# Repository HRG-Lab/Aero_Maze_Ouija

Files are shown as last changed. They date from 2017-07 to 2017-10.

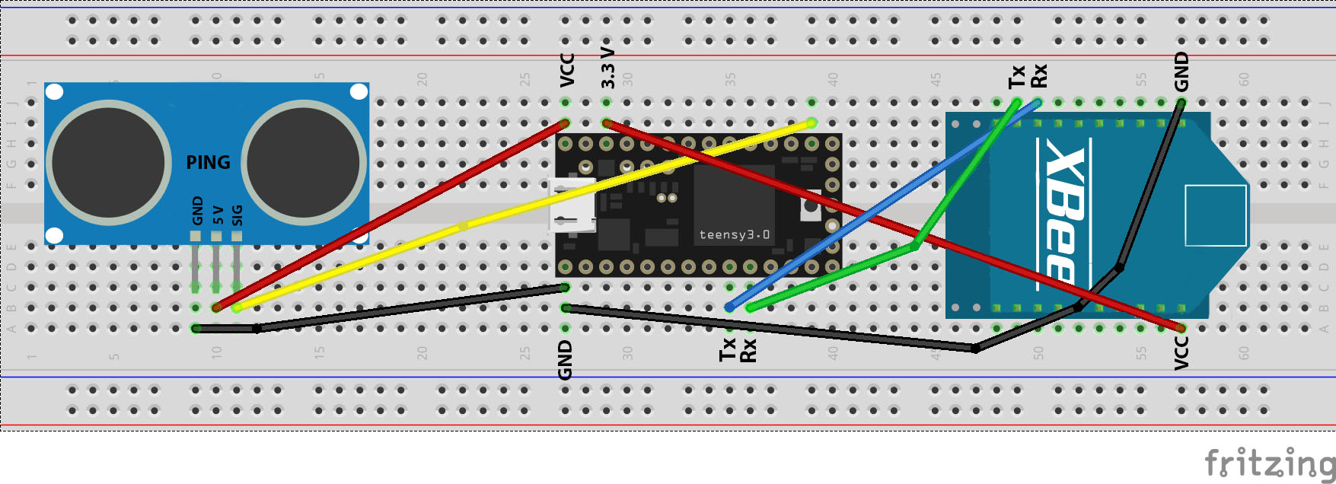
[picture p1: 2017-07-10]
Documentation/Ping_Sensor_Transmitter.jpg

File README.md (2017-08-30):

# Aero_Maze_Ouija #

### Description ###
The Aero Maze Ouija is an apparatus consisting of a group of sensors coordinating a hexacopter whose main body is a marble maze.
The project is intended to be used as a teambuilding exercise. The game, as designed, is meant for six players.
Each player will be assigned a distance sensor which will be used to measure the length between the sensor and each player's hand.
This data is then sent to the drone and mapped to a PWM value to control the speed of each motor.
Each of the six motors is linked to one specific sensor, so each player will be in control of one propeller.
There will be a maze etched into the drone where there will be a marble or bb.
The goal of the game is to work as a team and navigate the marble through the maze by controlling the orientation of the drone.

drone-overview

- - - -

## Required Software and Libraries ##
* Arduino v1.8.1
* XCTU to setup Xbee's
* Autodesk Fusion 360 (Optional, but you can size the maze we designed)
* Arduino Libraries:
  * Teesnyduino
  * EasyTransfer Library
  
- - - -

## Required Hardware ##
* A body for your drone, preferably made out of fiberglass
* 6 Turnigy Aerodrive D3536/9 910 KV Motors
* 6 Mounts designed for the Turnigy motors
* 6 Propellers, we used 3 1045's and 3 1045R's
* 6 Metal U channels
* An assortment of screws
* 7 xBees
* 6 ESC's, we used 6 Hobby King 30A UBEC's
* 3 Leg stands to attach to the U channels
* Xbee explorer board to
* Breadboard to mount electronics
* At least 8 pairs of XT60 connectors and the corresponding wires

- - - -

## Tools Needed for Assembly ##

* CNC Router to sketch the maze
* Power tools needed to drill holes etc.

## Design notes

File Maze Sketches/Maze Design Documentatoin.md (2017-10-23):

## Designing The Maze ##

* Using the software Autodesk Fusion 360 we have designed a marble maze that is based upon a Smith chart. Using the parameters menu one can easily reconfigure the size and dimensions of the maze to fit the almost any size board. One can easily find the software underneath Autodesk’s official website and receive a one month free trial to quickly generate an STL underneath any size they wish. The STL we have included in our files is a maze designed for a 14 inch diameter round piece of wood.

## Modifying the Maze ##

* In Autodesk Fusion 360, open the parameters menu and the main parameters the user will want to modify will be:
	* body_diameter - Set the diameter of your wood
	* trough_width - Set the width of the guiding structures of the maze
	* trough_depth - Set the depth of the guiding structures
	* end_hole_depth - Set the depth of the center hole in the maze
	* distance_guide - Is approximately the distance between the center of the neighboring guiding structure and the guiding structure that the former cuts off. One should tinker with this parameter to get the correct dimensions for their maze.

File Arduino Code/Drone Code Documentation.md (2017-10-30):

### Required Software ###
 
* Arduino 1.8.3 (https://www.arduino.cc/en/main/software)
* Teensyduino (https://www.pjrc.com/teensy/teensyduino.html)
* EasyTransfer Library (https://github.com/madsci1016/Arduino-EasyTransfer)
* XCTU (Source 8)
* AutoCAD Fusion 360 (https://www.autodesk.com/products/fusion-360/overview)
* Anaconda
* Pycharm
* PySerial

- - - -
 
## Setting up Software ##
 
* You will need to download and install Arduino 1.8.3 onto your computer if you do not already have Arduino installed. Leave all settings as default. Open up Arduino and try uploading a blank code to your device, or maybe a simple blink program. Make sure the right board is selected by going to Tools->Board:-> and select the device you are trying to upload the code to, such as Arduino Genuino/Uno, Teensy LC, or Teensy 3.0. 
* For Teensy 3.0 and Teensy LC it is necessary to have the Teensyduino downloaded. Do not change any of the settings or file locations when downloading Teensyduino, everything will be automatically setup for you.  When using Teensy 3.0 it will be necessary to change the frequency of the device by going to `Tools->CPU Speed:->` and changing it from 96 MHz (overclocked) to 48 MHz to avoid damaging the device. 
* The library EasyTransfer will need to be downloaded for this project and installed in the correct file. To do this find your Arduino folder stored in your hard drive at a location such as `c/Program Files (x86)/Arduino/library` and copy the unzipped EasyTransfer library into the library folder. 
* To configure the XBee’s you will need to have XCTU downloaded and installed on your computer. Download the latest version of XCTU and install it on your computer without changing any of the default settings. 

- - - -

### Motor Testing ###
* To test motors, wire pin 9 of the Arduino to the signal wire of the ESC and the ground wire of the Arduino to the ground wire of the ESC. Also, attach the servomotor and the power supply to the ESC. 

    
    
    *Pictured Above: Wiring of Servo Motor for testing*

* Upload the code to the Arduino and open the serial monitor. Type in a value and your motor’s speed will gradually rise or fall to match your entered value.

- - - -

## Programmming the ESC’s ##

* The arduino file underneath the filepath: `Arduino Code/Program ESC/ESCProgrammer/ESCProgrammer.ino` is designed to program the electronic speed controllers so that when the ESC’s are controlling the speed of the motors, the motors will turn on at roughly the same value and spin at similar rates.

1. Plug in an arduino to your computer and attach the ground port on the arduino to the ground pin (black wire) on the ESC PWM wires and port 9 on the arduino to the signal pin (white wire) on the ESC PWM wires. Also, attach power wires to the ESC.

    
    
    *Pictured Above: how to configure wires to ESC to program*

2. Before uploading the code, disconnect and reconnect the power supply to the ESC, this will allow the ESC to be programmed. Upload the code located in the aforementioned file path and upload this onto the board. Open the serial monitor and wait for the text “Done” to appear.

3. Repeat these steps on all the ESC’s until all are programmed.

- - - -

## Configure XBee setup ##

* Once XCTU installed connect the XBee using the XBee Explorer Dongle and open XCTU. Click on “Discover Radio Modules connected to your machine” and select the USB serial ports that show up. Click Next and then Click finish. If the device does not show up the first time you may need to select more Baud rates before clicking finish. Click “Add selected devices”, and then click on the selected device to configure it and access the console. The configuration settings used are pictured below. 

    
    
    *Pictured Above: The Settings window for XBee module displaying the settings we used*

* The only thing that was changed from the default was changing the Network ID from 7FFF to 8FFF. To communicate between two XBees select the console tab which is located right next to the settings tab and click the “Open/Close” button. This allows for you to see the messages sent by other networks on you console screen and send messages from the console screen to other XBees in the same network.

    
    
    *Pictured Above: Console window showing two XBees communicating with each other. The red text is from the other XBee, while the blue text is from the XBee that is connected to your device*

- - - -

## Configure Distance Transmission Setup ##

### Distance Sensor Setup ###

* Using a Teensy 3.0 or Teensy LC connect the distance sensor that is being used according to the following setup: Connect the GND pins to each other, the 5V pin to Vin on Teensy 3.0 or 5V on Teensy LC or Arduino Uno. Connect the signal pin (for the parallax 28015 ping ultrasonic range finder it is labeled SIG and for the XL-MaxSonar –EZ/AE Ultrasonic range finder it is pin 3) to an analog pin (In the code used in the project it is pin 14 for Teensy 3.0 and Teensy LC).

* For the parallax 28015 ping ultrasonic range finder we found code for measuring the distance at this link https://www.arduino.cc/en/Tutorial/Ping. This code relies on sending a pulse signal through the sensor and measuring the delay of the returning signal, and converting the time using the speed of sound to convert it into inches and centimeters. The code that was used in the project used the function to send out the pulse signal and convert it to centimeters. Pictured below is the sensor used.

    

* The code used in the project can be found at the filepath `Aero_Maze_Ouija/Arduino Code/Drone Code/Distance_Transmission_28015/Distance_Transmission_28015.ino`. This code provided accurate readings from 5cm to 80cm. If you are using this code for a board other than Teensy 3.0 or Teensy LC you may need to comment out lines involving Serial3 as this will cause an error when compiling. The distances will be displayed on the serial monitor.

* For the XL-MaxSonar –EZ/AE Ultrasonic range finder we created our own distance conversion code by taking in the signal using analogRead() to read in data from the pin connected to the sensor and printing the value to the serial monitor. We recorded the values produced by analogRead() along with the distances that we placed an object at from 95 cm to 20 cm every 5 cm (a limitation of this sensor is that it can not measure anything below 20 cm) plotted it to determine an equation that fit it, coming up with distance = (.6869*val)+2 where val is the integer value that is read in from analogRead().Below is a picture of this sensor.

    

* The code can be found at `Aero_Maze_Ouija/Arduino Code/Drone Code/Distance_Transmission_MAXSONAR/Distance_Transmission_MAXSONAR.ino` This code will provide fairly accurate readings (+- 3 cm)  from 20 cm to 95 cm. If this code does not seem as accurate as you would like you will need to go through the mapping process described above.

- - - -

## XBee Adaptor Connection ##

* This part requires an XBee adaptor board to connect the XBee to the Teensy. The one used in this project can be found here https://www.pjrc.com/store/xbee_adaptor.html. (Note: this page recommends that you do not use these boards for any new projects, but we used them in this project as we already them). Follow the steps outlined in this page to configure these for Teensy 2.0. It is important to follow the instructions outlined in the page for using it with Teensy LC or 3.0 as the boards were designed for the regulator chip to handle the 5V from the Teensy 2.0 or 2.0++, which means that for using with Teensy LC or 3.0 requires the 15k resistor to not be connected. Below is an image an adaptor showing the configuration used in this project.

    

* In the code you will also need to include the lines XBee xbee = XBee(); and Serial3.begin(9600). A test code used to verify  communication through the Teensys and XBee setup can be found at the file-path:
`Aero_Maze_Ouija/Arduino Code/Test Code/communication_Test/communication Test.ino`
	
* This code allows you to send messages to and from the serial monitor.

* To connect the adaptor board-XBee setup to the Teensy 3.0 or Teensy LC follow this diagram below:

- - - -

## Configure Distance Receiving/Motor Control Setup ##

### XBee Adaptor Connection ###

* See XBee Adaptor Connection under Configure Distance Transmission Setup

### Motor Connection Guide ###

* Each esc has a 3 input connection, the black wire will be connected to the ground of the Teensy and the white wire will be connected to the signal. Leave the middle red wire empty. Connect the signal wire to a pin on the Teensy (in our code we used pins 2-6 and 9).

    
    
    *Pictured Left: the three input connection: This is used in programming the esc and will be connected to the Teensy. Middle: This shows the wires from the Teensy connected to the three input connection (note that the green wires in this image represent the ground wire). Left: The esc with the input side (top) and output side to be connected to the motors (bottom)*

* The code for receiving the packets of data and sending out a signal to the motors can be found under the file-path:
`Aero_Maze_Ouija/Arduino Code/Drone Code/_6_Motors_Recieving/_6_Motors_Recieving.ino`

* The red and black power cables on the input side of the esc  will be connect to power and ground of the power supply respectively. On the output side of the esc the connection cables should alternate the connection between the black and colored wires, with red still going to red. So the setup would be red-red, blue-yellow, black-black; and for the next esc-motor setup it should be red-red, black-yellow, blue-black. This can be seen in the picture below. 

    
    
    *Pictured Left: Showing the connection red-red, blue-black, black-yellow. Pictured Right: Showing the connection red-red, blue-yellow, black-black*

* It incorporates the easy transfer library to receive the distances and an identifying character from each setup, and then case structures to select between the different characters and control individual motors.

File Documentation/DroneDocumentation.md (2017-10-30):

#### Areo-Smith Maze  ####



### Aerosmith Maze ###
* Diameter: 48 cm
* Thickness: 1.2 cm
 
 - - - -

### Overview ###
 &nbsp;&nbsp;For this project, the goal was to build a maze that a small metal bb pellet could navigate. This was done mainly through the use of teensy microcontrollers, ultrasonic sensors, ESC motors and xbee radio modules.
&nbsp;&nbsp;The maze outline, resembling a smith chart, was carved into a large, round piece of plexiglass with a CNC machine. Six ESC motors are attached to this piece of plexiglass, which tilt the maze in various directions, based on how fast each motor is spinning. This is how the bb navigates the maze, as each motor receives data from an ultrasonic sensor which tells it how fast or slow to spin. Each ultrasonic sensor will output a distance measurement based on how close or far an object is to it. The distance value that each sensor outputs is sent to a teensy microcontroller, which is programmed to send the data through an XBee module. The data is sent wirelessly to another XBee on the receiving end, which is connected to another teensy. This teensy is attached to the plexiglass maze, and is programmed to control all of the 6 motors, based on the different values it receives from each of the 6 sensors.
&nbsp;&nbsp;The maze is designed to be controlled by 6 different people at one time, with each person controlling one motor by moving their hands in front of an ultrasonic sensor. Based on how the teensys were programmed, the closer your hand is to the ultrasonic sensor, the faster the motor will spin. Therefore, to tilt the maze up in one direction, one person will have to move their hand closer to the ultrasonic sensor that corresponds to that specific motor. The maze is attached to a ball and socket joint which is tethered to a tripod, which allows it the freedom to rotate in any direction, without the maze flying away due to the lift of the motors. This project was designed to encourage people to work together to complete a task, and the maze is best navigated when the speed of one motor is changed at a time.
&nbsp;&nbsp;This document will outline the materials needed and the steps that should be  taken in order to build the Aerosmith maze, and a list of references that was used will be included at the end.

### Required Materials ###
* 1 Round piece of wood 
* 6 Turnigy Aerodrives motors (D3536/9 910KV) (https://hobbyking.com/en_us/turnigy-d3536-9-910kv-brushless-outrunner-motor.html)
* 6 Electronic Speed controllers (Hobby King 30A UBEC) (https://hobbyking.com/en_us/hobby-king-30a-esc-3a-ubec.html)
* 6 Propellors: 3 1045R, 3 1045 (https://www.newegg.com/Product/Product.aspx?Item=9SIA2RP0XW3805)
* 6 Metal Channels (http://www.johnsonrollforming.com/display.php/display/A1/category/2)
* 3 3D printed legs
* 6 3D printed motor mounts
* 6 Metal cross brackets for motor mounts (http://www.crlaurence.com/crlapps/showline/offerpage.aspx?ProductID=11909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)
* 1 power supply (BK precision 1900) (http://www.bkprecision.com/products/power-supplies/1900-1-16v-60a-switching-dc-power-supply.html)
* 7 breadboards 16.5 cm x 5.5 cm (https://www.itead.cc/breadboard-16-5-x-5-5cm.html)
* 7 XBee PRO S1 With Antennas (https://www.sparkfun.com/products/8742)
* 7 Teensy LC or Teensy 3.0 (https://www.pjrc.com/teensy/teensyLC.html)
* 7 Teensy to XBee Adaptor kits (https://www.sparkfun.com/products/13311)
* 6 parallax 28015 ping ultrasonic range finder or XL-MaxSonar –EZ/AE Ultrasonic range finder (https://www.parallax.com/product/28015)
* XBee Explorer Dongle (https://www.sparkfun.com/products/11697)
* Assorted nuts and screws

### Required Software ###
 
* Arduino 1.8.3 (https://www.arduino.cc/en/main/software)
* Teensyduino (https://www.pjrc.com/teensy/teensyduino.html)
* EasyTransfer Library (https://github.com/madsci1016/Arduino-EasyTransfer)
* XCTU (Source 8)
* AutoCAD Fusion 360 (https://www.autodesk.com/products/fusion-360/overview)
* Anaconda
* Pycharm
* PySerial

- - - -
 
## Setting up Software ##
 
* You will need to download and install Arduino 1.8.3 onto your computer if you do not already have Arduino installed. Leave all settings as default. Open up Arduino and try uploading a blank code to your device, or maybe a simple blink program. Make sure the right board is selected by going to Tools->Board:-> and select the device you are trying to upload the code to, such as Arduino Genuino/Uno, Teensy LC, or Teensy 3.0. 
* For Teensy 3.0 and Teensy LC it is necessary to have the Teensyduino downloaded. Do not change any of the settings or file locations when downloading Teensyduino, everything will be automatically setup for you.  When using Teensy 3.0 it will be necessary to change the frequency of the device by going to `Tools->CPU Speed:->` and changing it from 96 MHz (overclocked) to 48 MHz to avoid damaging the device. 
* The library EasyTransfer will need to be downloaded for this project and installed in the correct file. To do this find your Arduino folder stored in your hard drive at a location such as `c/Program Files (x86)/Arduino/library` and copy the unzipped EasyTransfer library into the library folder. 
* To configure the XBee’s you will need to have XCTU downloaded and installed on your computer. Download the latest version of XCTU and install it on your computer without changing any of the default settings. 

- - - -

### Motor Testing ###
* To test motors, wire pin 9 of the Arduino to the signal wire of the ESC and the ground wire of the Arduino to the ground wire of the ESC. Also, attach the servomotor and the power supply to the ESC. 

    
    
    *Pictured Above: Wiring of Servo Motor for testing*

* Upload the code to the Arduino and open the serial monitor. Type in a value and your motor’s speed will gradually rise or fall to match your entered value.

- - - -

## Programmming the ESC’s ##

* The arduino file underneath the filepath: `Arduino Code/Program ESC/ESCProgrammer/ESCProgrammer.ino` is designed to program the electronic speed controllers so that when the ESC’s are controlling the speed of the motors, the motors will turn on at roughly the same value and spin at similar rates.

1. Plug in an arduino to your computer and attach the ground port on the arduino to the ground pin (black wire) on the ESC PWM wires and port 9 on the arduino to the signal pin (white wire) on the ESC PWM wires. Also, attach power wires to the ESC.

    
    
    *Pictured Above: how to configure wires to ESC to program*

2. Before uploading the code, disconnect and reconnect the power supply to the ESC, this will allow the ESC to be programmed. Upload the code located in the aforementioned file path and upload this onto the board. Open the serial monitor and wait for the text “Done” to appear.

3. Repeat these steps on all the ESC’s until all are programmed.

- - - -

## Configure XBee setup ##

* Once XCTU installed connect the XBee using the XBee Explorer Dongle and open XCTU. Click on “Discover Radio Modules connected to your machine” and select the USB serial ports that show up. Click Next and then Click finish. If the device does not show up the first time you may need to select more Baud rates before clicking finish. Click “Add selected devices”, and then click on the selected device to configure it and access the console. The configuration settings used are pictured below. 

    
    
    *Pictured Above: The Settings window for XBee module displaying the settings we used*

* The only thing that was changed from the default was changing the Network ID from 7FFF to 8FFF. To communicate between two XBees select the console tab which is located right next to the settings tab and click the “Open/Close” button. This allows for you to see the messages sent by other networks on you console screen and send messages from the console screen to other XBees in the same network.

    
    
    *Pictured Above: Console window showing two XBees communicating with each other. The red text is from the other XBee, while the blue text is from the XBee that is connected to your device*

- - - -

## Configure Distance Transmission Setup ##

### Distance Sensor Setup ###

* Using a Teensy 3.0 or Teensy LC connect the distance sensor that is being used according to the following setup: Connect the GND pins to each other, the 5V pin to Vin on Teensy 3.0 or 5V on Teensy LC or Arduino Uno. Connect the signal pin (for the parallax 28015 ping ultrasonic range finder it is labeled SIG and for the XL-MaxSonar –EZ/AE Ultrasonic range finder it is pin 3) to an analog pin (In the code used in the project it is pin 14 for Teensy 3.0 and Teensy LC).

* For the parallax 28015 ping ultrasonic range finder we found code for measuring the distance at this link https://www.arduino.cc/en/Tutorial/Ping. This code relies on sending a pulse signal through the sensor and measuring the delay of the returning signal, and converting the time using the speed of sound to convert it into inches and centimeters. The code that was used in the project used the function to send out the pulse signal and convert it to centimeters. Pictured below is the sensor used.

    

* The code used in the project can be found at the filepath `Aero_Maze_Ouija/Arduino Code/Drone Code/Distance_Transmission_28015/Distance_Transmission_28015.ino`. This code provided accurate readings from 5cm to 80cm. If you are using this code for a board other than Teensy 3.0 or Teensy LC you may need to comment out lines involving Serial3 as this will cause an error when compiling. The distances will be displayed on the serial monitor.

* For the XL-MaxSonar –EZ/AE Ultrasonic range finder we created our own distance conversion code by taking in the signal using analogRead() to read in data from the pin connected to the sensor and printing the value to the serial monitor. We recorded the values produced by analogRead() along with the distances that we placed an object at from 95 cm to 20 cm every 5 cm (a limitation of this sensor is that it can not measure anything below 20 cm) plotted it to determine an equation that fit it, coming up with distance = (.6869*val)+2 where val is the integer value that is read in from analogRead().Below is a picture of this sensor.

    

* The code can be found at `Aero_Maze_Ouija/Arduino Code/Drone Code/Distance_Transmission_MAXSONAR/Distance_Transmission_MAXSONAR.ino` This code will provide fairly accurate readings (+- 3 cm)  from 20 cm to 95 cm. If this code does not seem as accurate as you would like you will need to go through the mapping process described above.

- - - -

## XBee Adaptor Connection ##

* This part requires an XBee adaptor board to connect the XBee to the Teensy. The one used in this project can be found here https://www.pjrc.com/store/xbee_adaptor.html. (Note: this page recommends that you do not use these boards for any new projects, but we used them in this project as we already them). Follow the steps outlined in this page to configure these for Teensy 2.0. It is important to follow the instructions outlined in the page for using it with Teensy LC or 3.0 as the boards were designed for the regulator chip to handle the 5V from the Teensy 2.0 or 2.0++, which means that for using with Teensy LC or 3.0 requires the 15k resistor to not be connected. Below is an image an adaptor showing the configuration used in this project.

    

* In the code you will also need to include the lines XBee xbee = XBee(); and Serial3.begin(9600). A test code used to verify communication through the Teensys and XBee setup can be found at the file-path:
`Aero_Maze_Ouija/Arduino Code/Test Code/communication_Test/communication Test.ino`
	
* This code allows you to send messages to and from the serial monitor.

* To connect the adaptor board-XBee setup to the Teensy 3.0 or Teensy LC follow this diagram below:

- - - -

## Configure Distance Receiving/Motor Control Setup ##

### XBee Adaptor Connection ###

* See XBee Adaptor Connection under Configure Distance Transmission Setup

### Motor Connection Guide ###

* Each esc has a 3 input connection, the black wire will be connected to the ground of the Teensy and the white wire will be connected to the signal. Leave the middle red wire empty. Connect the signal wire to a pin on the Teensy (in our code we used pins 2-6 and 9).

    
    
    *Pictured Left: the three input connection: This is used in programming the esc and will be connected to the Teensy. Middle: This shows the wires from the Teensy connected to the three input connection (note that the green wires in this image represent the ground wire). Left: The esc with the input side (top) and output side to be connected to the motors (bottom)*

* The code for receiving the packets of data and sending out a signal to the motors can be found under the file-path:
`Aero_Maze_Ouija/Arduino Code/Drone Code/_6_Motors_Recieving/_6_Motors_Recieving.ino`

* The red and black power cables on the input side of the esc  will be connect to power and ground of the power supply respectively. On the output side of the esc the connection cables should alternate the connection between the black and colored wires, with red still going to red. So the setup would be red-red, blue-yellow, black-black; and for the next esc-motor setup it should be red-red, black-yellow, blue-black. This can be seen in the picture below. 

    
    
    *Pictured Left: Showing the connection red-red, blue-black, black-yellow. Pictured Right: Showing the connection red-red, blue-yellow, black-black*

* It incorporates the easy transfer library to receive the distances and an identifying character from each setup, and then case structures to select between the different characters and control individual motors.

## Designing The Maze ##

* Using the software Autodesk Fusion 360 we have designed a marble maze that is based upon a Smith chart. Using the parameters menu one can easily reconfigure the size and dimensions of the maze to fit the almost any size board. One can easily find the software underneath Autodesk’s official website and receive a one month free trial to quickly generate an STL underneath any size they wish. The STL we have included in our files is a maze designed for a 14 inch diameter round piece of wood.

## Modifying the Maze ##

* In Autodesk Fusion 360, open the parameters menu and the main parameters the user will want to modify will be:
	* body_diameter - Set the diameter of your wood
	* trough_width - Set the width of the guiding structures of the maze
	* trough_depth - Set the depth of the guiding structures
	* end_hole_depth - Set the depth of the center hole in the maze
	* distance_guide - Is approximately the distance between the center of the neighboring guiding structure and the guiding structure that the former cuts off. One should tinker with this parameter to get the correct dimensions for their maze.

## Producing 3D Printed Housing ##

* Using Autodesk Fusion 360 
* These can be found under the filepath Aero_Maze_Ouija->3D Printed Parts
	* The housing for the sensors consisted of a 3D printed box and lid seen below: Dimensions 8.5cm by 7.5cm by 7.4cm.
	
        
	* Brackets were made for the maze to be mounted on as seen below: &nbsp;&nbsp; &nbsp;&nbsp; &nbsp;&nbsp; &nbsp;&nbsp; &nbsp;&nbsp; &nbsp;&nbsp; &nbsp;&nbsp; &nbsp;&nbsp;&nbsp;&nbsp; &nbsp;&nbsp; &nbsp;&nbsp; &nbsp;&nbsp;
	
	
	
	
	* Casing for the recieving and motor control setup were made to house the wires

## Finialized Product ##

* Below are pictures depicting the final product:




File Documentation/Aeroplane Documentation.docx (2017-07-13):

Aerosmith Maze

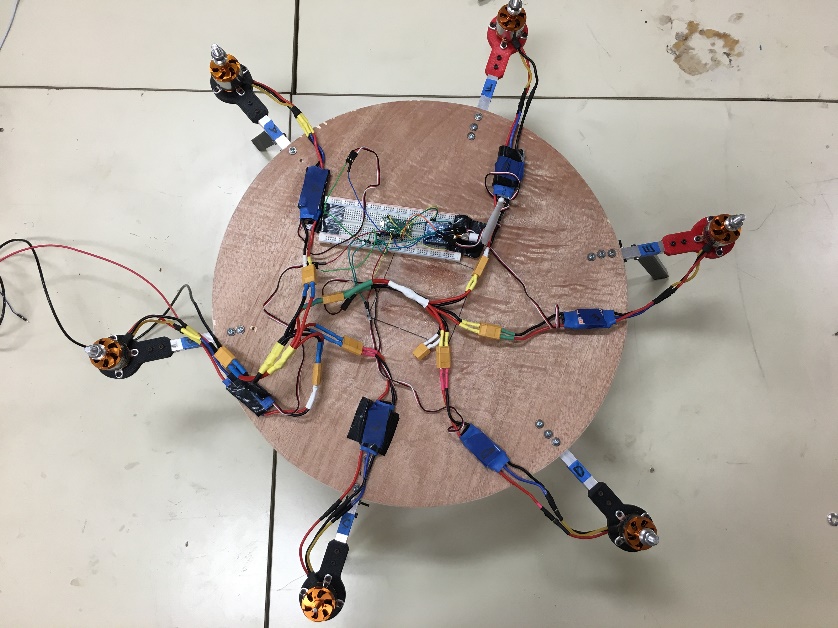
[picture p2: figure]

Diameter: 48 cm

Thickness: 1.2 cm

Materials

1 Round piece of wood

6 Turnigy Aerodrives motors (D3536/9 910KV)

6 Electronic Speed controllers (Hobby King 30A UBEC)

1 power supply (BK precision 1900)

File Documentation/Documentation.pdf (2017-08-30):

# Aerosmith Maze

### Texas A&M University

### HRG

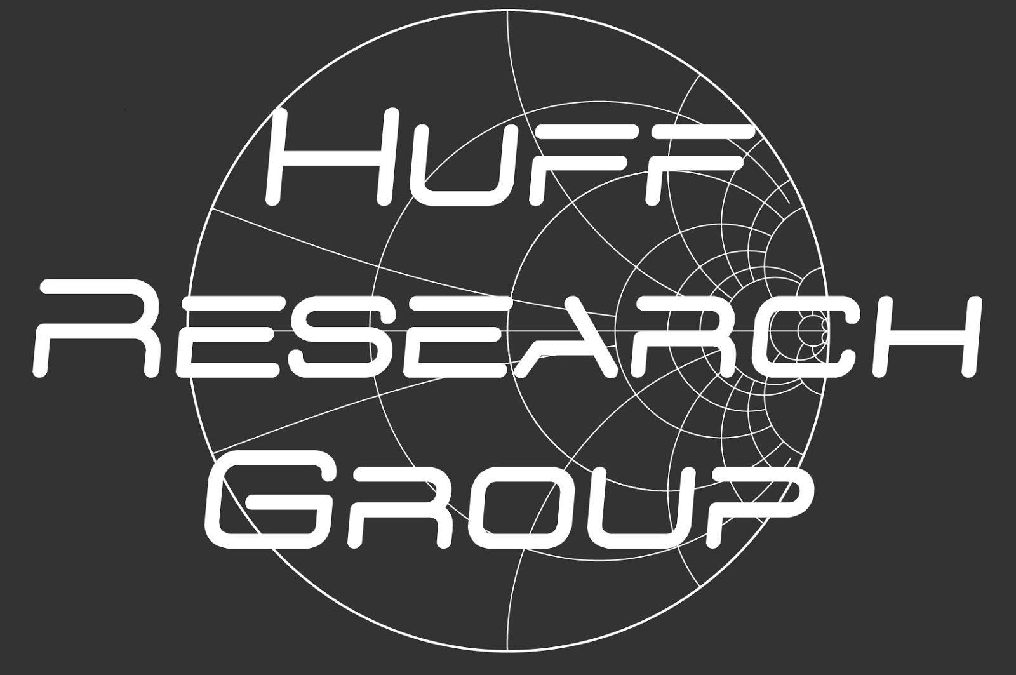
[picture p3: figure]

TABLE | OF | CONTENTS
Distance | Transmission | Configuration | /

### Overview

For this project, the goal was to build a maze that a small metal bb pellet could navigate. This was done mainly through the use of teensy microcontrollers, ultrasonic sensors, ESC motors and xbee radio modules.
The maze outline, resembling a smith chart, was carved into a large, round piece of plexiglass with a CNC machine. Six ESC motors are attached to this piece of plexiglass, which tilt the maze in various directions, based on how fast each motor is spinning. This is how the bb navigates the maze, as each motor receives data from an ultrasonic sensor which tells it how fast or slow to spin. Each ultrasonic sensor will output a distance measurement based on how close or far an object is to it. The distance value that each sensor outputs is sent to a teensy microcontroller, which is programmed to send the data through an XBee module. The data is sent wirelessly to another XBee on the receiving end, which is connected to another teensy. This teensy is attached to the plexiglass maze, and is programmed to control all of the 6 motors, based on the different values it receives from each of the 6 sensors.
The maze is designed to be controlled by 6 different people at one time, with each person controlling one motor by moving their hands in front of an ultrasonic sensor. Based on how the teensys were programmed, the closer your hand is to the ultrasonic sensor, the faster the motor will spin. Therefore, to tilt the maze up in one direction, one person will have to move their hand closer to the ultrasonic sensor that corresponds to that specific motor. The maze is attached to a ball and socket joint which is tethered to a tripod, which allows it the freedom to rotate in any direction, without the maze flying away due to the lift of the motors. This project was designed to encourage people to work together to complete a task, and the maze is best navigated when the speed of one motor is changed at a time. This document will outline the materials needed and the steps that should be taken in order to build the Aerosmith maze, and a list of references that was used will be included at the end.

### Materials

- 1 Round piece of plexiglass
- 6 Turnigy Aerodrives motors (D3536/9 910KV)
- 6 Electronic Speed controllers (Hobby King 30A UBEC)
- 6 Propellers: 3 1045R, 3 1045
- 6 Metal Channels
- 3 3D printed legs
- 6 3D printed motor mounts
- 6 Metal cross brackets for motor mounts
- 1 power supply (BK precision 1900)
- 7 breadboards 16.5 cm x 5.5 cm
- 7 XBee PRO S1 With Antennas
- 7 Teensy LC or Teensy 3.0
- 7 Teensy to XBee Adaptor kits
- 6 parallax 28015 ping ultrasonic range finder or XL-MaxSonar –EZ/AE Ultrasonic range finder
- XBee Explorer Dongle
- 1 ball and socket joint
- Assorted nuts and screws

### Software

- Arduino 1.8.3 (https://www.arduino.cc/en/main/software)
- Teensyduino (https://www.pjrc.com/teensy/teensyduino.html)
- EasyTransfer Library
(https://github.com/madsci1016/Arduino-EasyTransfer)
- XCTU (Source 8)
- AutoCAD Fusion 360
(https://www.autodesk.com/products/fusion-360/overview)
- Anaconda
- Pycharm
- PySerial

Setting | up | the | Software

You will need to download and install Arduino 1.8.3 onto your computer if you do not already have Arduino installed. Leave all settings as default. Open up Arduino and try uploading a blank code to your device, or maybe a simple blink program. Make sure the right board is selected by going to Tools->Board:-> and select the device you are trying to upload the code to, such as Arduino Genuino/Uno, Teensy LC, or Teensy 3.0. Also under Tools->USB Type:-> make sure that “Serial is selected and under Tools->Port-> make sure the specific device that is being uploaded to is selected. When using the Arduino it is necessary for the Rx1 and Tx1 pin to be clear and not connected to anything when uploading code to the device or an error will appear.

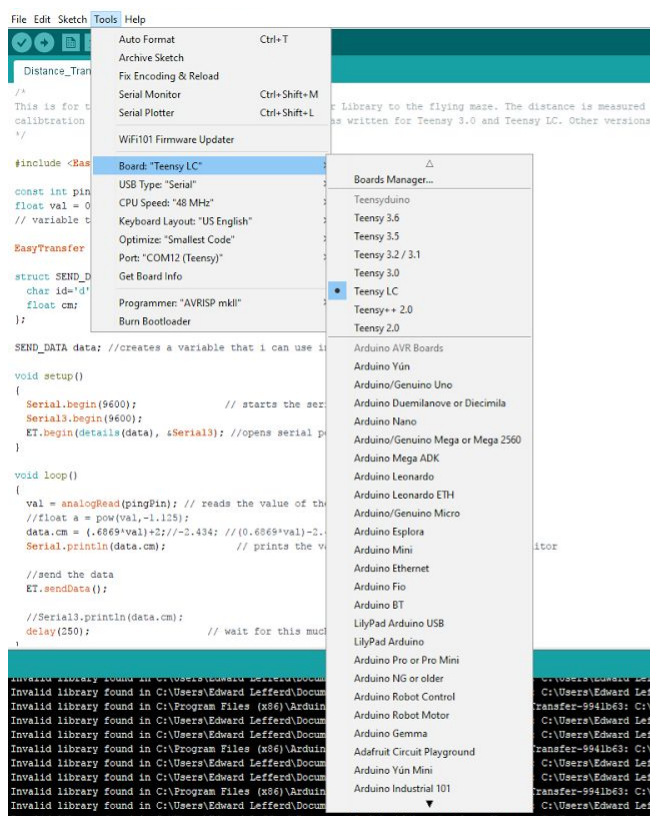
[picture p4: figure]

Pictured Above: Tool Bar Settings in Arduino For Teensy 3.0 and Teensy LC it is necessary to have the Teensyduino downloaded. Do not change any of the settings or file locations when downloading Teensyduino, everything will be automatically setup for you. When using Teensy 3.0 it is necessary to change the frequency from 96 MHz (overclocked) to 48 MHz to avoid damaging the device by going to Tools->CPU Speed:->

The library EasyTransfer will need to be downloaded for this project and installed in the correct file. To do this find your Arduino folder stored in your hard drive at a location such as c/Program Files (x86)/Arduino/library and copy the unzipped EasyTransfer library into the library folder. If an error occurs about the library when trying to run/compile the code it may be necessary to remove the individual EasyTransfer libraries from the main unzipped file and place them in the library file separately.
To configure the XBees you will need to have XCTU downloaded and installed on your computer. Download the latest version of XCTU and install it on your computer without changing any of the default settings.

### Motor Testing

To test motors, wire pin 9 of the Arduino to the signal wire of the ESC and the ground wire of the Arduino to the ground wire of the ESC. Also, attach the servomotor and the power supply to the ESC.

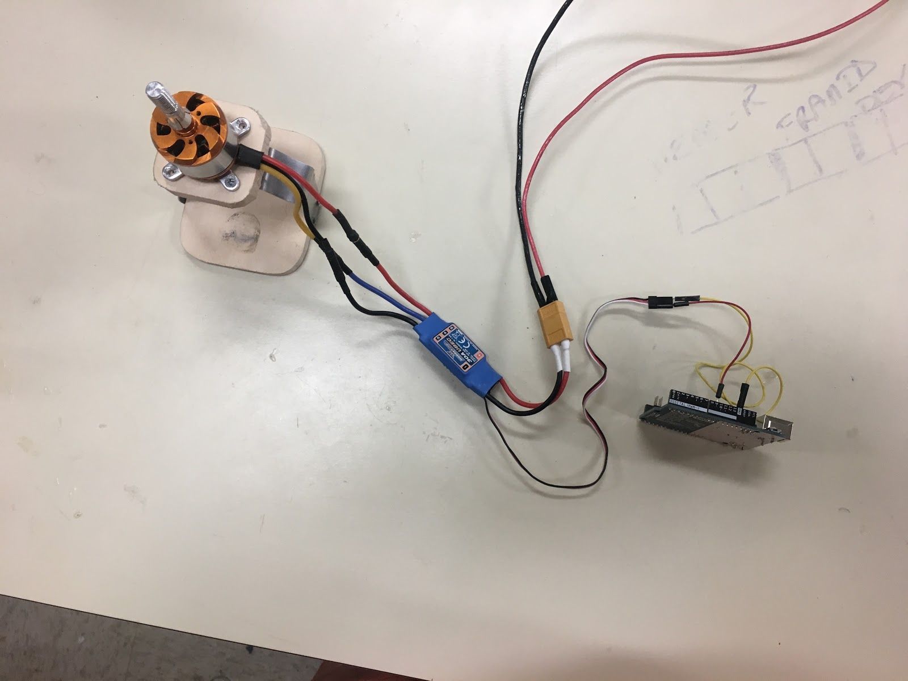
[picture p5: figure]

Pictured Above: Wiring of Servo Motor for testing

Upload the code to the Arduino and open the serial monitor. It can be found under the filepath Arduino Code->Test Code->Motor_Test->Motor_Test.ino. Type in a value and your motor’s speed will gradually rise or fall to match your entered value.

Programming | the | ESC’s

The arduino file underneath the filepath: Arduino Code->Program ESC->ESCProgrammer->ESCProgrammer.ino, is designed to program the electronic speed controllers so that when the ESC’s are controlling the speed of the motors, the motors will turn on at roughly the same value and spin at similar rates.

1. Plug in an arduino to your computer and attach the ground port on the arduino to the ground pin (black wire) on the ESC PWM wires and port 9 on the arduino to the signal pin (white wire) on the ESC PWM wires. Also, attach power wires to the ESC.

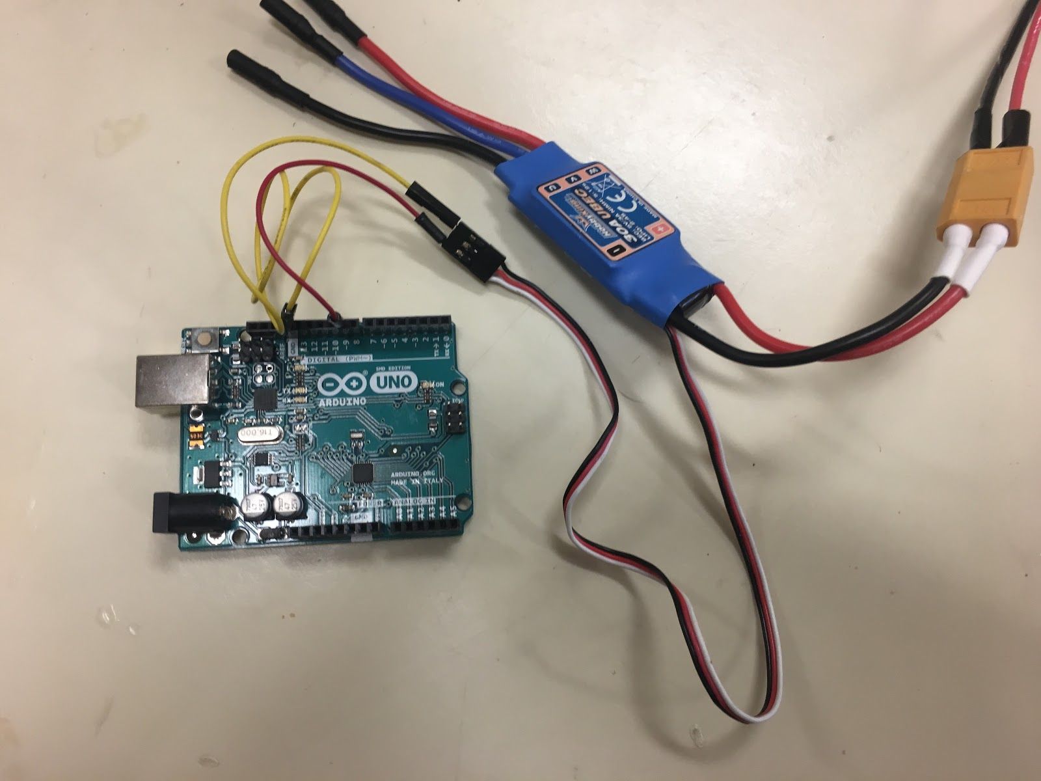
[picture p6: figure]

Pictured Above: how to configure wires to ESC to program

2. Before uploading the code, disconnect and reconnect the power supply to the ESC, this will allow the ESC to be programmed. Upload the code located in the aforementioned file path and upload this onto the board. Open the serial monitor and wait for the text “Done” to appear.
3. Repeat these steps on all the ESC’s until all are programmed.

XBee | Configuration/ | Setup

Once XCTU installed connect the XBee using the XBee Explorer Dongle and open XCTU. Click on “Discover Radio Modules connected to your machine” and select the USB serial ports that show up. Click Next and then Click finish. If the device does not show up the first time you may need to select more Baud rates before clicking finish. Click “Add selected devices”, and then click on the selected device to configure it and access the console. A window my appear that says that the device needs to be reset, in which case the pin in the bottom of the board marked “RST” must be connect to the pin marked “GND”. If the XBee does not show up when searching for devices, and resetting it does not work the XBee may be broken and it would be best to try a different one. The configuration settings used are pictured below.

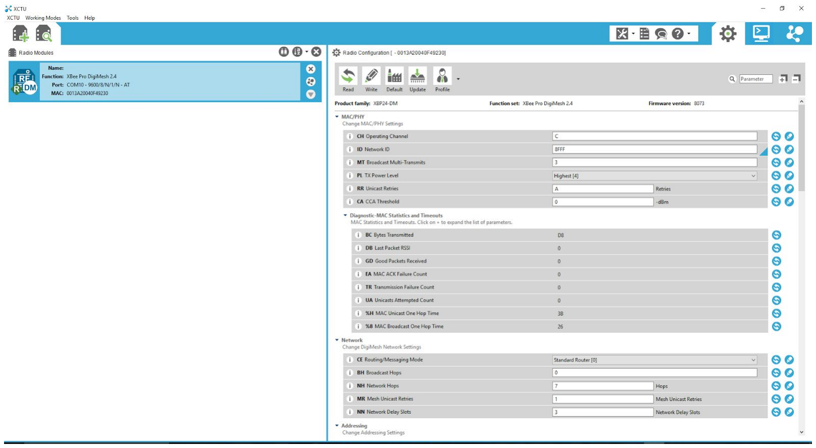
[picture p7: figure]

Pictured Above: The Settings window for XBee module displaying the settings we used

The only thing that was changed from the default was changing the Network ID from 7FFF to 8FFF. To communicate between two XBees select the console tab located next to the settings tab and click the “Open/Close” button. This allows for you to see the messages sent by other networks on your console screen and send messages from the console screen to other XBees in the same network.

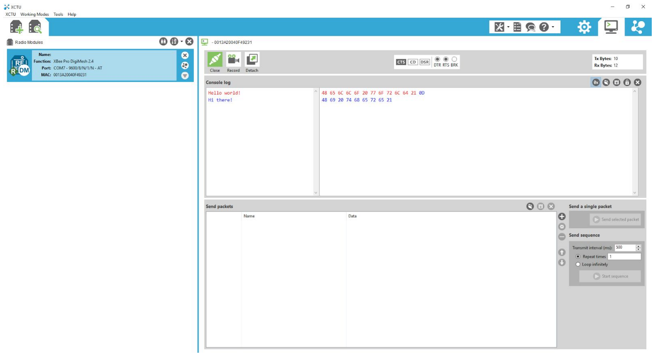
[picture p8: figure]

Pictured Above: Console window showing two XBees communicating with each other. The red text is from the other XBee, while the blue text is from the XBee that is connected to your device.

Distance | Transmission | Configuration/ | Setup

Distance Sensor Setup

Using a Teensy 3.0 or Teensy LC connect the distance sensor that is being used according to the following setup: Connect the GND pins to each other, the 5V pin to Vin on Teensy 3.0 or 5V on Teensy LC or Arduino Uno. Connect the signal pin (for the parallax 28015 ping ultrasonic range finder it is labeled SIG and for the XL-MaxSonar –EZ/AE Ultrasonic range finder it is pin 3) to an analog pin (In the code used in the project it is pin 14 for Teensy 3.0 and Teensy LC).

For the parallax 28015 ping ultrasonic range finder we found code for measuring the distance at this link https://www.arduino.cc/en/Tutorial/Ping . This code relies on sending a pulse signal through the sensor and measuring the delay of the returning signal, and converting the time using the speed of sound to convert it into inches and centimeters. The code used in the project used the function to send out the pulse signal and converted it to centimeters. Pictured below is the sensor used.

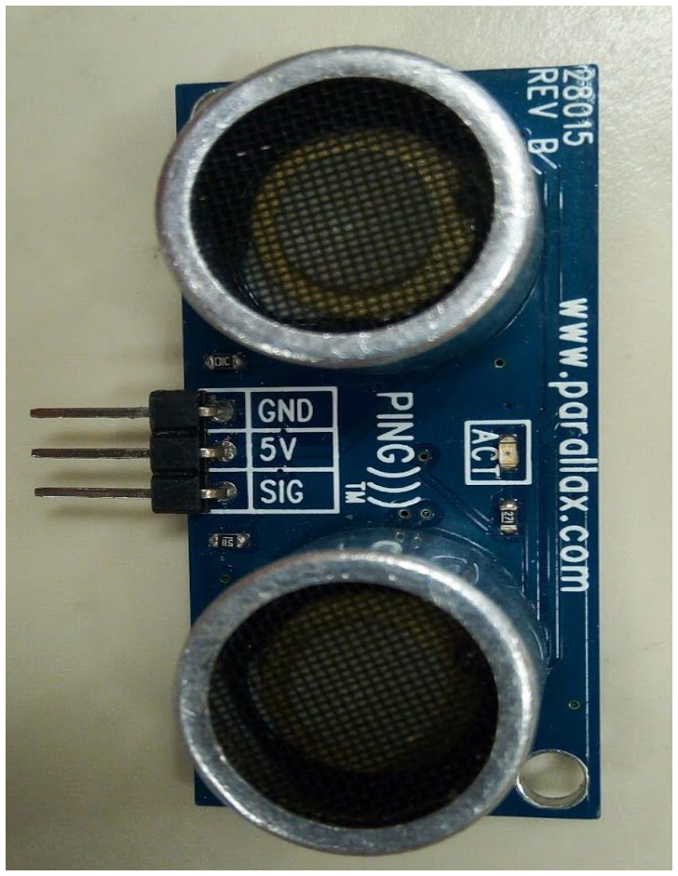
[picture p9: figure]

The code used in the project can be found at the filepath Aero_Maze_Ouija->Arduino Code->Drone Code->Distance_Transmission_28015->Distance_Transmission_28015.ino. This code provides accurate readings from 5cm to 80cm. If you are using this code for a board other than Teensy 3.0 or Teensy LC you may need to comment out lines involving Serial3 as this will cause an error when compiling. The distances will be displayed on the serial monitor.

For the XL-MaxSonar –EZ/AE Ultrasonic range finder we created our own distance conversion code by taking in the signal using analogRead() to read in data from the pin connected to the sensor and printing the value to the serial monitor. We recorded the values produced by analogRead() along with the distances that we placed an object at from 95 cm to 20 cm every 5 cm (a limitation of this sensor is that it can not measure anything below 20 cm) plotted it to determine an equation that fit it, coming up with distance = (.6869*val)+2 where val is the integer value that is read in from analogRead(). This mapping function was created for the Teensy LC and Teensy 3.0. When used with a different device, such as an Arduino Uno, the values produced by analogRead() are different and require a new mapping function to be created. Below is a picture of this sensor.

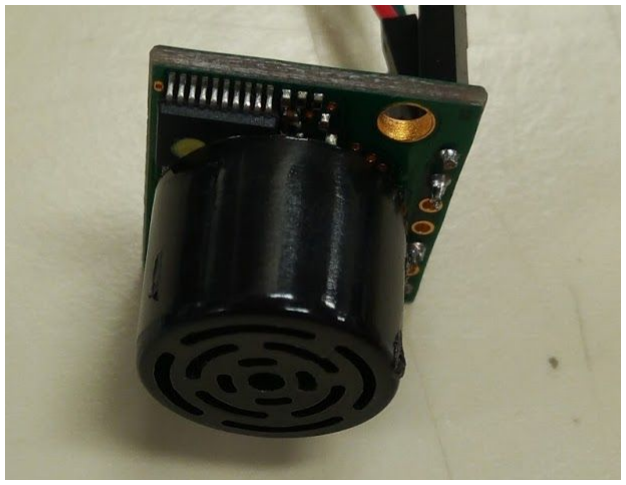
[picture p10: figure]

The code can be found at Aero_Maze_Ouija->Arduino Code->Drone Code->Distance_Transmission_MAXSONAR->Distance_Transmission_MAXSO NAR.ino. This code will provide fairly accurate readings (+- 3 cm) from 20 cm to

95 cm. If this code does not seem as accurate as you would like you will need to go through the mapping process described above.

XBee Adaptor Connection
This part requires an XBee adaptor board to connect the XBee to the Teensy. The one used in this project can be found here https://www.pjrc.com/store/xbee_adaptor.html. (Note: this page recommends that you do not use these boards for any new projects, but we used them in this project as we already had them). Follow the steps outlined in this page to configure these for Teensy 2.0. It is important to follow the instructions outlined in the page for using it with Teensy LC or 3.0 as the boards were designed for the regulator chip to handle the 5V from the Teensy 2.0 or 2.0++, which means that for using the Teensy LC or 3.0 requires the 15k resistor to not be connected. Below is an image an adaptor showing the configuration used in this project. The 15k resistor is removed and the two connections below the 10k resistor go from the middle pins to the left pins (without the ++).

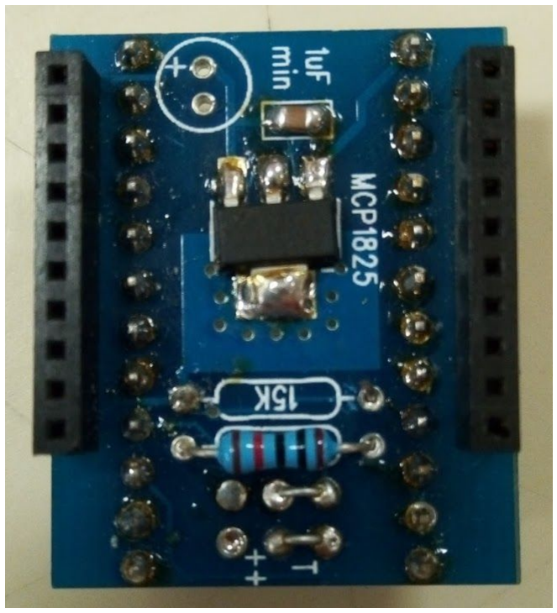
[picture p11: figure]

In the code you will also need to include the lines XBee xbee = XBee(); and Serial3.begin(9600). A test code we used to verify that we could communicate through the Teensys and XBee setup can be found at the file-path Aero_Maze_Ouija->Arduino Code->Test Code->communication_Test->communication_Test.ino. This code allows you to send messages to and from the serial monitor. It serves as a simple test and does not require the sensors to be setup as it sends and receives strings of text.
When you examine this code you may notice that it includes both Serial and Serial3. Serial is connected to the serial monitor on the Teensy/Arduino that is being used. Serial3 is used for Rx3 and Tx3 which are the data that is being sent out through the XBee and received through the XBee. Rx3 and Tx3 are used with the Teensies because of the specific adaptor board used requires that Rx3 and Tx3 be used if using anything higher than a Teesny 2.0 or 2.0++. If using a different type of Adaptor board which allows for the use of Rx1 and Tx1, then use Serial instead of Serial3.

To connect the adaptor board-XBee setup to the Teensy 3.0 or Teensy LC follow the diagram below:

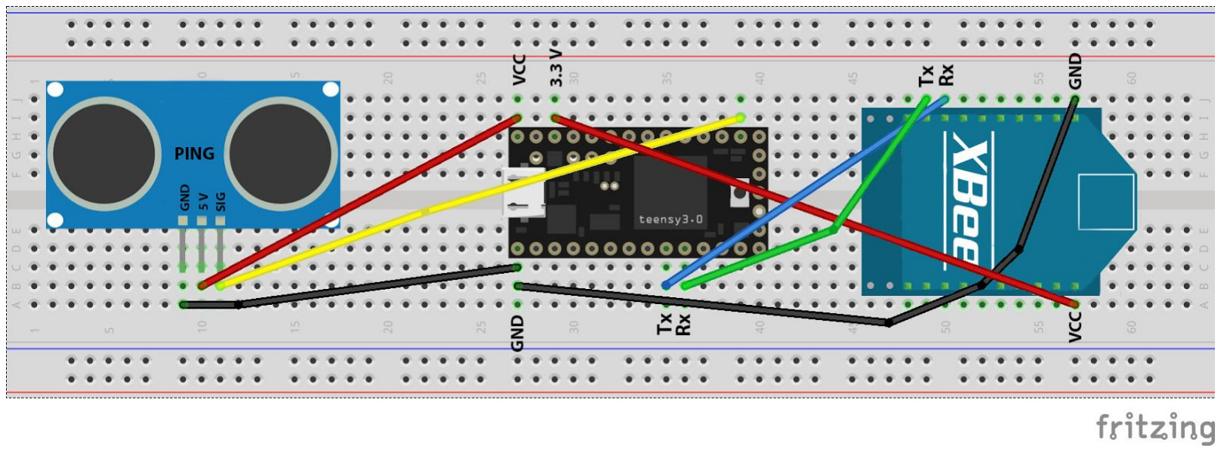
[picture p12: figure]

To complete the distance transmission setup simply use the code from the Distance Sensor Setup section and make sure that the XBee and distance sensor are connected as outlined above.
Configure | Distance | Receiving/Motor | Control | Setup

XBee Adaptor Connection

See XBee Adaptor Connection under Configure Distance Transmission Setup

Motor Connection Guide

Each esc has a 3 input connection: leaving the middle red wire empty, the black wire is connected to the ground of the Teensy and the white wire is connected to the signal pin on the Teensy (in our code we used pins 2-6 and 9).

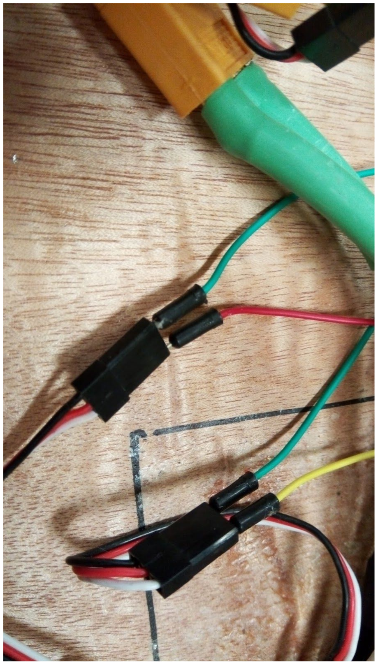
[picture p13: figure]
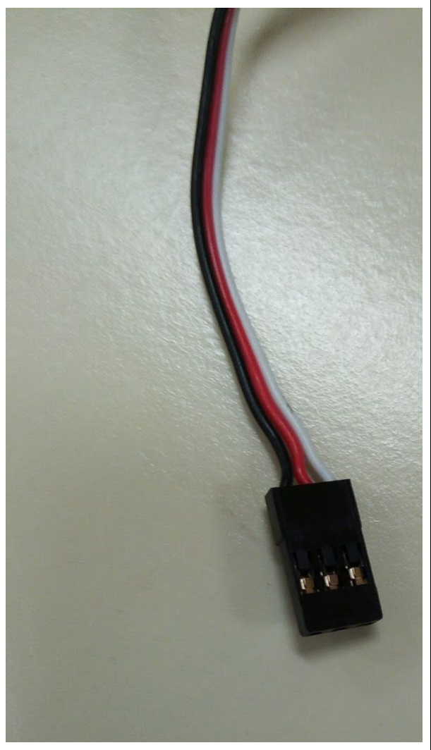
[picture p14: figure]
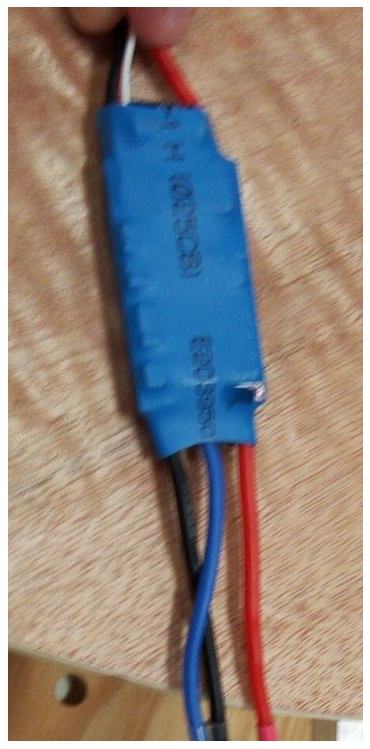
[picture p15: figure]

Pictured Left: the three input connection: This is used in programming the esc and will be connected to the Teensy.
Middle: This shows the wires from the Teensy connected to the three input connection (note that the green wires in this image represent the ground wire).
Right: The esc with the input side (top) and output side to be connected to the motors (bottom)

The code for receiving the packets of data and sending out a signal to the motors can be found under the file-path Aero_Maze_Ouija->Arduino Code->Drone Code-> _6_Motors_Recieving->_6_Motors_Recieving.ino.
The red and black power cables on the input side of the esc will be connect to power and ground of the power supply respectively. On the output side of the esc the connection cables should alternate the connection between the black and colored wires, with red still going to red.
So the setup would be red-red,blue-yellow,black-black; and for the next esc-motor setup it should be red-red,black-yellow,blue,black. This can be seen in the picture below.

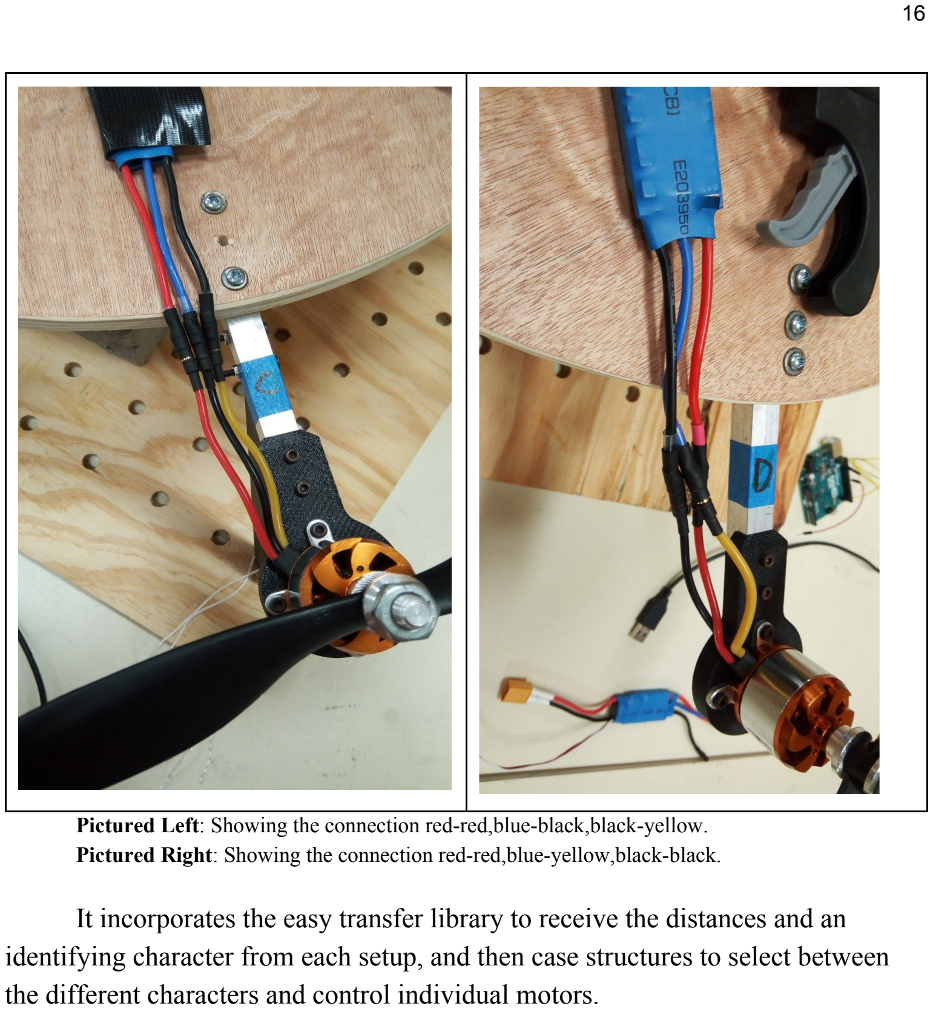
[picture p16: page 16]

Pictured | Left: Showing the connection red-red,blue-black,black-yellow.
Pictured | Right: Showing the connection red-red,blue-yellow,black-black.

It incorporates the easy transfer library to receive the distances and an identifying character from each setup, and then case structures to select between the different characters and control individual motors.

Designing | The | Maze
Using the software Autodesk Fusion 360 we designed a marble maze that is based upon a Smith chart. Using the parameters menu, one can easily reconfigure the size and dimensions of the maze to fit the almost any size board. One can easily find the software underneath Autodesk’s official website and receive a one month free trial to quickly generate an STL underneath any size they wish. The STL we have included in our files is a maze designed for a 14 inch diameter round piece of fiberglass.

Modifying the Maze
In Autodesk Fusion 360, open the parameters menu and the main parameters the user will want to modify will be:
- body_diameter - Set the diameter of your wood
- trough_width - Set the width of the guiding structures of the maze
- trough_depth - Set the depth of the guiding structures
- end_hole_depth - Set the depth of the center hole in the maze
- distance_guide - Is approximately the distance between the center of the neighboring guiding structure and the guiding structure that the former cuts off. One should tinker with this parameter to get the correct dimensions for their maze.

Mounting the Maze
Mounting the maze to the tripod requires a lot of different parts that attach to each other. First, a 3D printed tripod mount will attach to the tripod, which will have the ball and socket joint attached to it. A metal rod screws into the ball and socket joint, which will be attached to the bottom of the maze. A 3D printed funnel will then go onto the metal rod, and have holes for 6 different wooden dowels, one for each motor. Each motor is connected to the maze with a metal bar, and to this bar there will be attached a dowel holder. This will hold the wooden dowel for each motor that attaches to the funnel. Each part has been pictured below with the included dimensions. The dowel holder, funnel, and tripod mount was 3D printed, while the ball and socket joint and wooden dowels were purchased at a store.

Dowel Holder:
Inner Diameter: 1cm
Height: 3.6cm
Lower Width: 11.5 cm
Angle of tube = 23˚ from horizontal

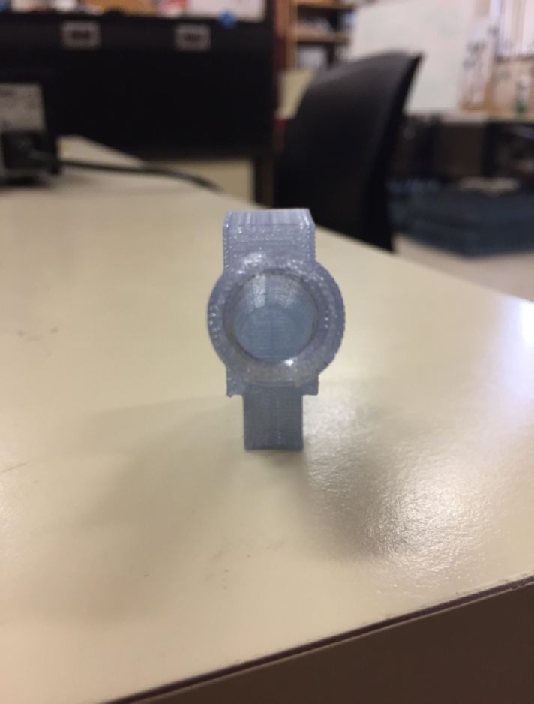
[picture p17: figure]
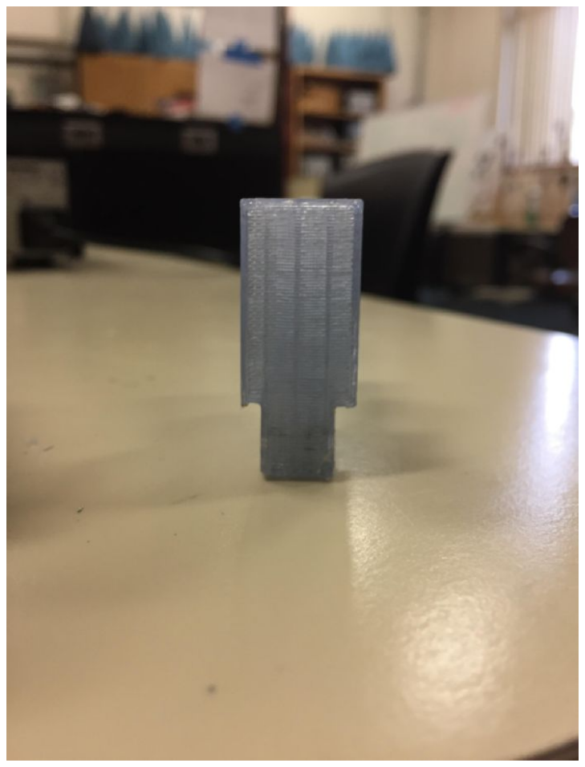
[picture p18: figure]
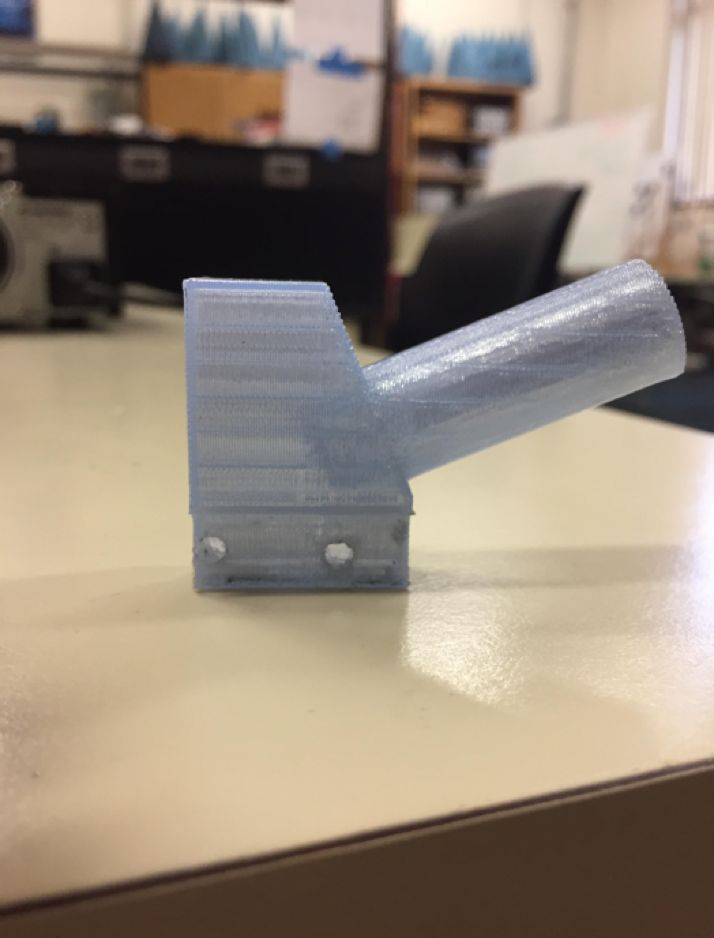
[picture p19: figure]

### Final Product

Sensor Boxes
Length: 8.5 cm
Width: 7.4 cm
Height: 7.5 cm

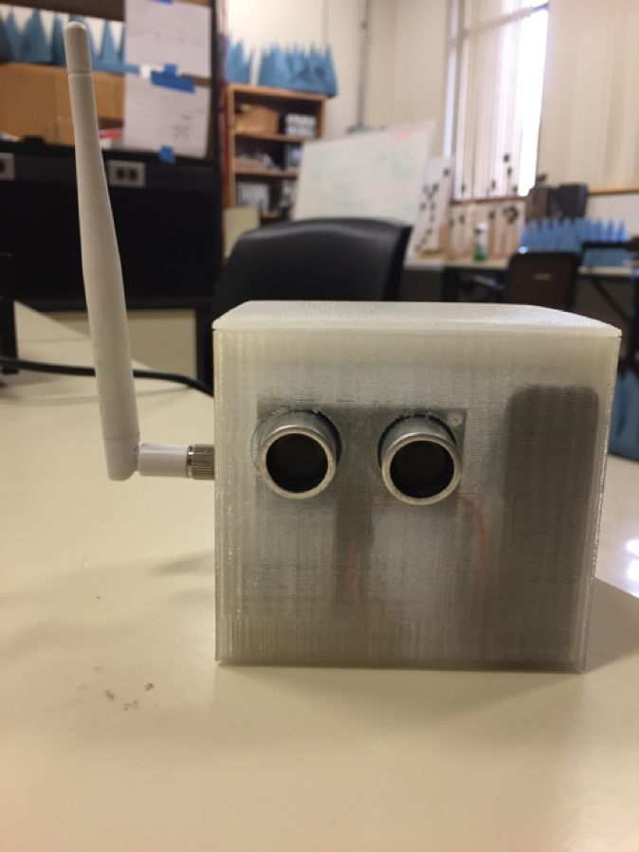
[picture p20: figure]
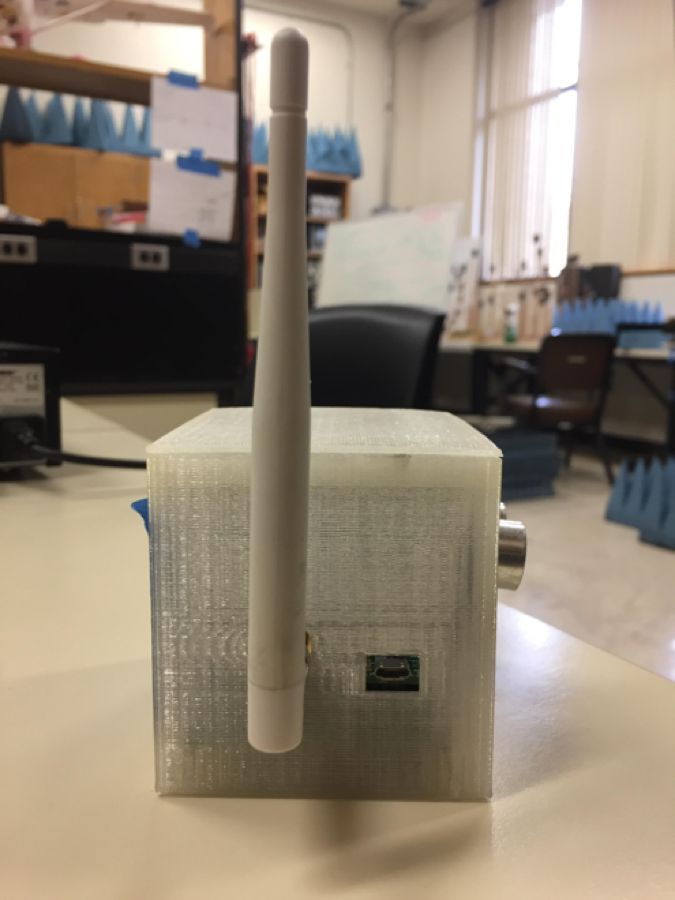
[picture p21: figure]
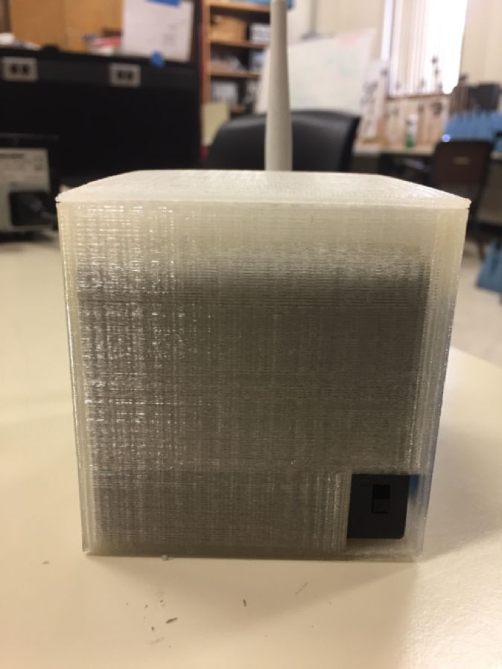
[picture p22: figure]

### 6 Sensor boxes were 3D printed. Each box contains an ultrasonic sensor and an

XBee with an antenna, both of which are connected to a teensy.

### References

Websites for purchasing materials:
6 Turnigy Aerodrives motors (D3536/9 910KV) (https://hobbyking.com/en_us/turnigy-d3536-9-910kv-brushless-outrunner-motor.h tml)
- 6 Electronic Speed controllers (Hobby King 30A UBEC) (https://hobbyking.com/en_us/hobby-king-30a-esc-3a-ubec.html)
- 6 Propellors: 3 1045R, 3 1045 (https://www.newegg.com/Product/Product.aspx?Item=9SIA2RP0XW3805)
- 6 Metal Channels
(http://www.johnsonrollforming.com/display.php/display/A1/category/2)
6 Metal cross brackets for motor mounts (http://www.crlaurence.com/crlapps/showline/offerpage.aspx?ProductID=11909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)
- 1 power supply (BK precision 1900) (http://www.bkprecision.com/products/power-supplies/1900-1-16v-60a-switching-dc-power-supply.html)
- 7 breadboards 16.5 cm x 5.5 cm (https://www.itead.cc/breadboard-16-5-x-5-5cm.html)
- 7 XBee PRO S1 With Antennas (https://www.sparkfun.com/products/8742)
- 7 Teensy LC or Teensy 3.0 (https://www.pjrc.com/teensy/teensyLC.html)
- 7 Teensy to XBee Adaptor kits (https://www.sparkfun.com/products/13311)
- 6 parallax 28015 ping ultrasonic range finder or XL-MaxSonar –EZ/AE Ultrasonic range finder (https://www.parallax.com/product/28015)
- XBee Explorer Dongle (https://www.sparkfun.com/products/11697)

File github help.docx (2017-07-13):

SETUP GITHUB

1. Download git on: https://git-scm.com/downloads

You can either download git or the the git gui client.

1. Go to github and click on clone or download and copy the URL

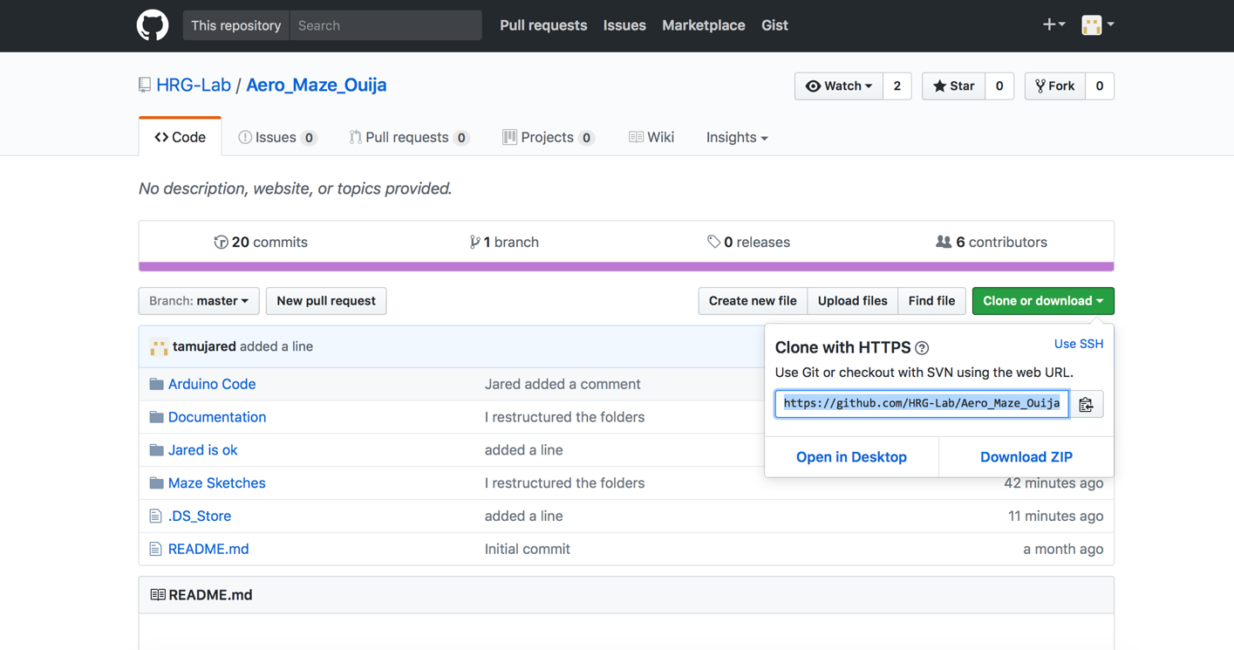
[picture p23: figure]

2. Go to either terminal (Mac) or gitbash (PC) and navigate to your folder you want to place the github repository in.

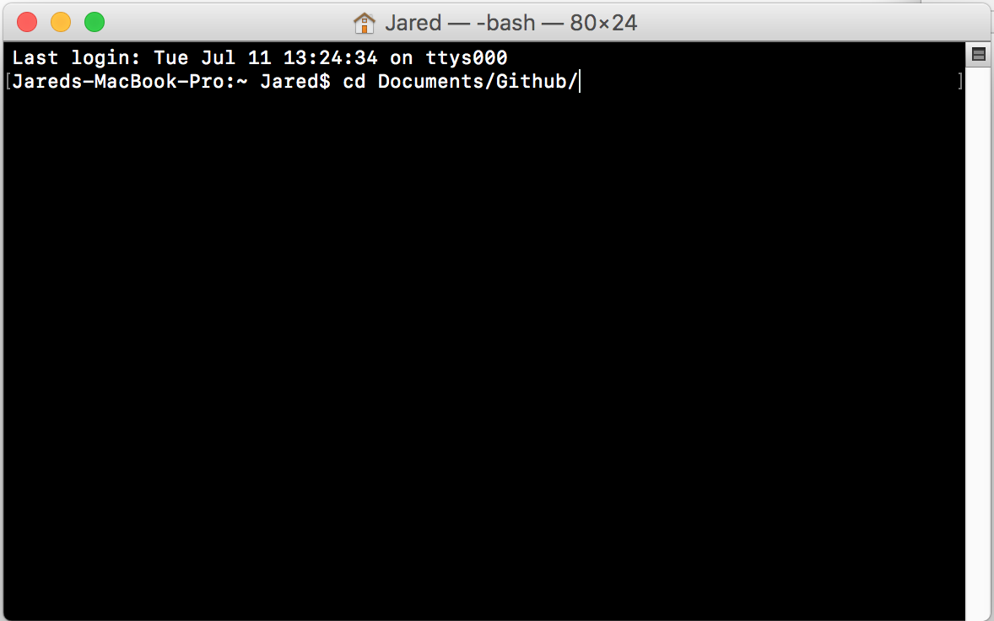
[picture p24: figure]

3. Type in git clone website where “website” is the link you copied earlier

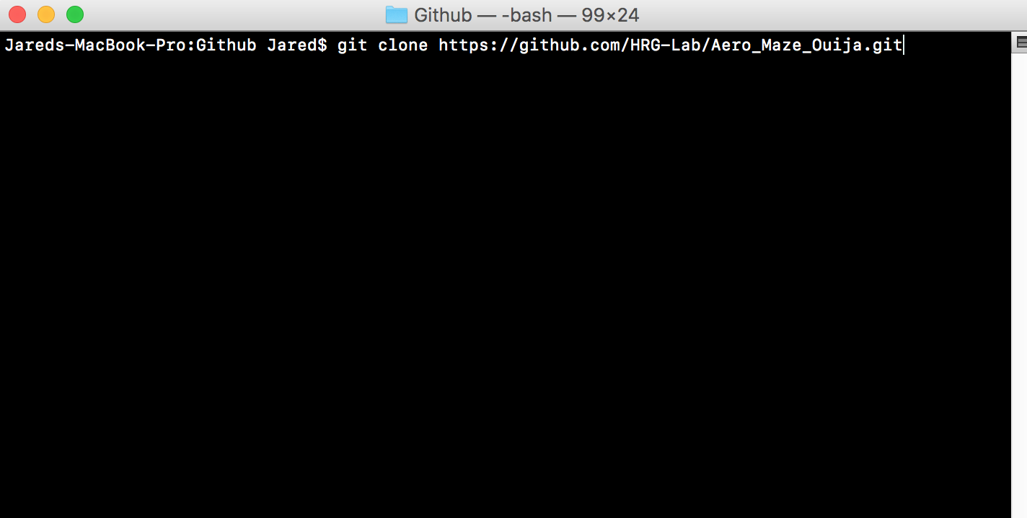
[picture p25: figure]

Your files should be set up, so if you go back to your file browser on your computer, everything will be there.

RETRIEVE FILES UPDATED FILES

In order to update to the latest version of the files type in git pull this will pull the information onto your computer

SEND YOUR UPDATED FILES

- In github type in git add -A this says that we will update all the files
- Type in git commit -m ”Put your comments here”
- Type in git push this will push your documents to the repository

TIPS

-You use git status to view the status

-If you get stuck executing a program try pressing control-z

-use this link to learn how to navigate your files: http://www.ee.surrey.ac.uk/Teaching/Unix/

-Use cd to change directory

-Use cd .. to back out of a directory

-Use ls to view the contents of the directory

FAQ

-If you need to change your home directory type in:

setx HOME "your\path\to\home"

and change “home” to the file path you want it to be (i.e. /c/users/Username)

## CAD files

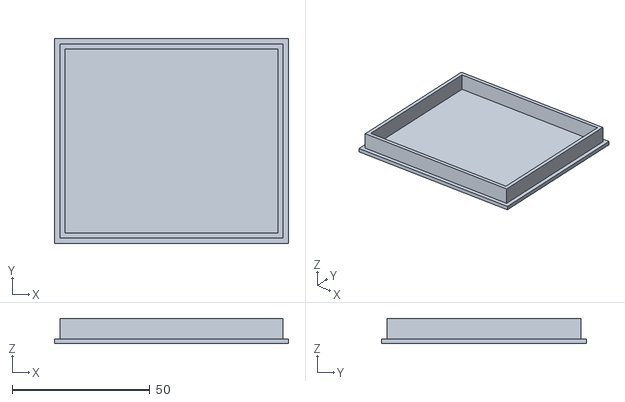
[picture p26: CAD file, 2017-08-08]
3D Printed Parts/lid_for_box3.0.stl
85.0 x 74.5 x 9.25

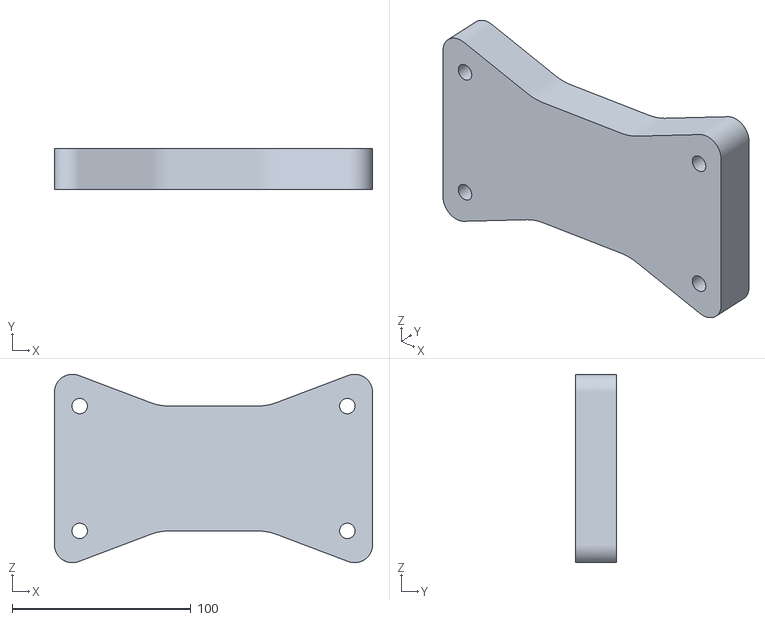
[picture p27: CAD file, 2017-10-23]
Models/Bottom Mount.stl
177.8 x 22.9 x 105.3

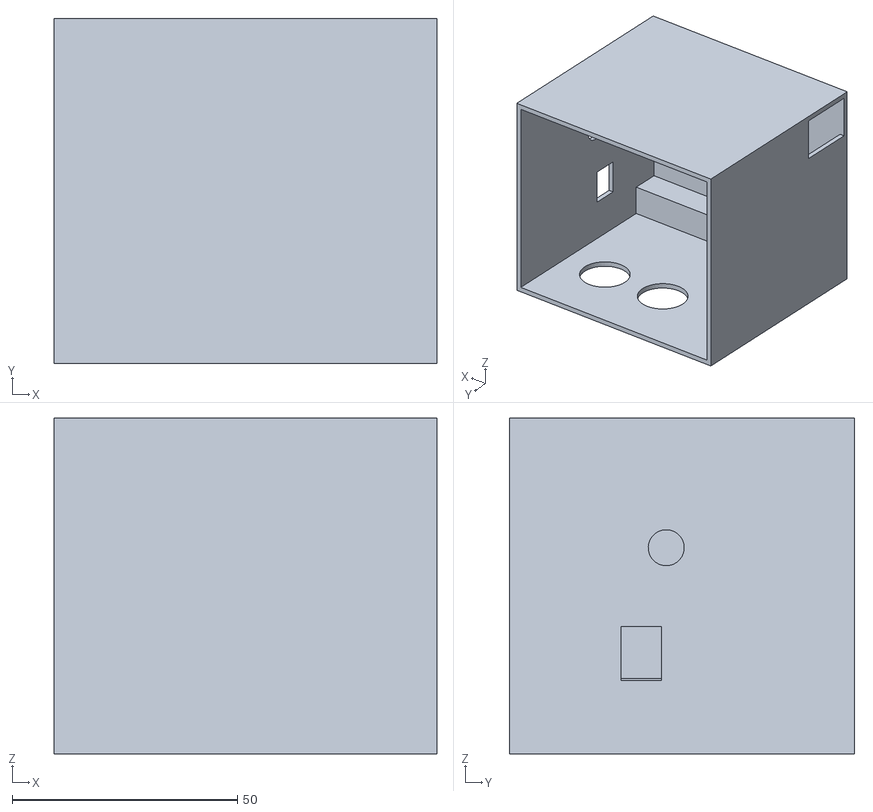
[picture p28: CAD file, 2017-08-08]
3D Printed Parts/Sensor_Enclosure-v3.0.stl
85.0 x 76.5 x 74.5

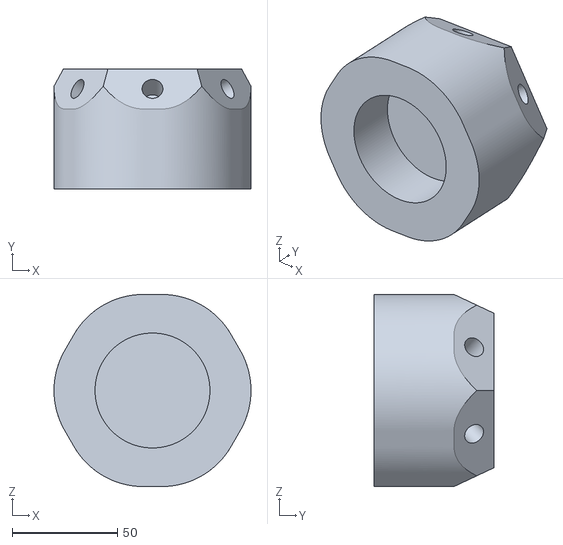
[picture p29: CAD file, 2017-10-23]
Models/Cone Top.stl
93.6 x 57.2 x 91.3

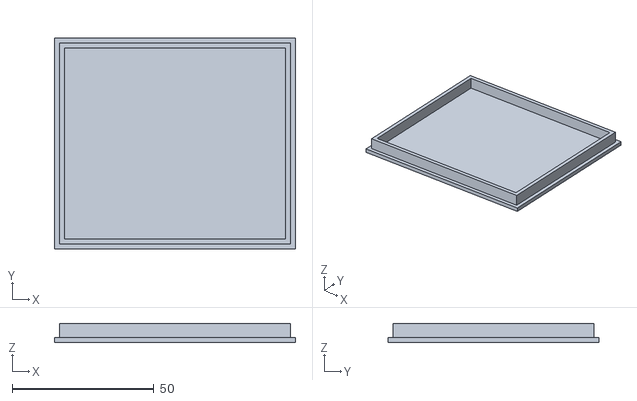
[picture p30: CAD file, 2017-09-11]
Models/lid_for_box2.0.stl
85.0 x 74.5 x 6.75

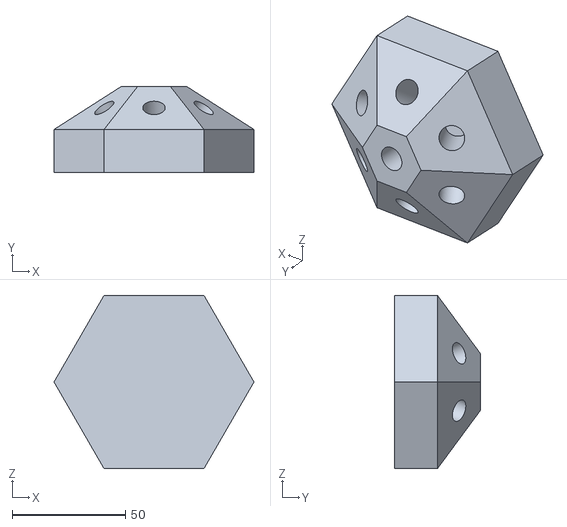
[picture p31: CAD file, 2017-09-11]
Models/Maze_Cone.stl
88.2 x 38.1 x 76.4

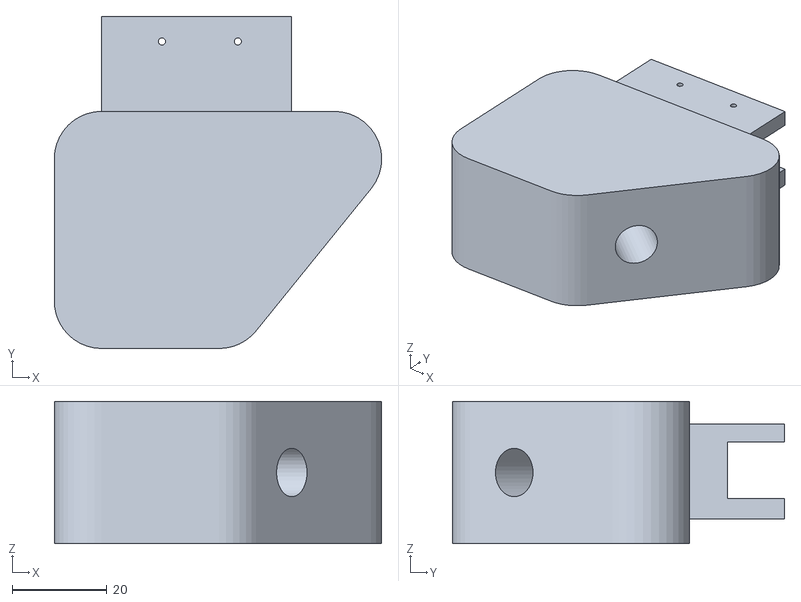
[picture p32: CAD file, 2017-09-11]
Models/Assem2STL - Part9^Assem2-1.STL
69.0 x 70.0 x 30.0

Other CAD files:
Models/Maze Sketches/Resizable_Smith_Chart_Complete_7-18.f3d
Models/Maze Sketches/SMITH_FINAL_MODEL v0.f3d

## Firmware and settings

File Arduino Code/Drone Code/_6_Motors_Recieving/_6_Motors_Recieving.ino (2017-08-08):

/*
 This code is for the recieving structure that controls all six motors attached to the body of the flying maze. The motors are initialized and throttled in the setup procedure. A data stucture called "data" is recieved containing an identifying character "data.id" and
 distance "data.cm" from each ultrasonic sensor setup. If the distance is less than 80cm it will turn the motor on, increasing motor rpm until it reaches 5cm. If the distance recieved is not less than 80cm or is 0cm the motor will have a default value written to it that 
 puts it in the "off" state. The code was written for the Teensy 3.0 and Teensy LC. For different versions of Teensy and Arduino the Serial3 port may need to be changed.
 */
#include <Servo.h>
#include <EasyTransfer.h>
#include <XBee.h>

//create object
Servo esc;
Servo esc2;
Servo esc3;
Servo esc4;
Servo esc5;
Servo esc6;
XBee xbee = XBee();
EasyTransfer ET; 
int value;
int dist_low=5;//lower bound of distance for 20815 transmit: declared for all motors. Change depending where you want your lower bound to be
int dist_low2=20;//lower bound of distance for MAXSONAR transmit: declared for all motors. Change depending on where you want your lower bound to be
int dist_high=80;//upper bound of distance for 20815 transmit: declared for all motors. Change depending where you want your upper bound to be
int dist_high2=95;//upper bound of distance for MAXSONAR transmit: declared for all motors. Change depending on where you want your upper bound to be
int motor_low=600;//lower bound of motor speed: declared for all motors. Change depending where the motor turn on point is
int motor_high=1450;//upper bound of motor speed: declared for all motors. Change depending where the motor max speed is
int val_default=500;//default motor speed for off: declared for all motors. Change as needed to value that motor is not on yet. 0 does not work for this
//Rx16Response rx16 = Rx16Response();

//recieved data structure is from each sensor transmission setup, including an identifying character
//a-b-c-d-e-f and the distance
struct RECEIVE_DATA_STRUCTURE{
  //put your variable definitions here for the data you want to receive
  //THIS MUST BE EXACTLY THE SAME ON THE OTHER ARDUINO
  char id;
  float cm;
};


RECEIVE_DATA_STRUCTURE data;

void setup(){
  Serial.begin(9600);
  Serial3.begin(9600);
  xbee.setSerial(Serial3);
  xbee.begin(Serial3);
  //follwing lines are for setting up the motors
  esc.attach(2); //Specify the esc signal pin,Here as D8
  esc2.attach(3);
  esc3.attach(4);
  esc4.attach(5);
  esc5.attach(6);
  esc6.attach(9);
  value=0; 
  esc.writeMicroseconds(value);
  esc2.writeMicroseconds(value);
  esc3.writeMicroseconds(value);
  esc4.writeMicroseconds(value);
  esc5.writeMicroseconds(value);
  esc6.writeMicroseconds(value);
  //Serial.println(value);
  delayMicroseconds(500000);
  value=val_default;
  esc.writeMicroseconds(value);
  esc2.writeMicroseconds(value);
  esc3.writeMicroseconds(value);
  esc4.writeMicroseconds(value);
  esc5.writeMicroseconds(value);
  esc6.writeMicroseconds(value);
  //Serial.println(value);
  delayMicroseconds(500000);
  
  
  //start the library, pass in the data details and the name of the serial port. Can be Serial, Serial1, Serial2, etc. 
  ET.begin(details(data), &Serial3);
  //pinMode(13, OUTPUT);
  
}
float val,  rssi1;
float val2, rssi2;
float val3, rssi3;
float val4, rssi4;
float val5, rssi5;
float val6, rssi6;
float data1=0;
float data2=0;
float data3=0;
float data4=0;
float data5=0;
float data6=0;
void loop(){
  //check and see if a data packet has come in.
  //each case controls a single motor dependent on the recieved "id" character in the recieved data struct "data"

  if(ET.receiveData()){
    //case 'a' 'b' 'c' dist_low and dist_high bounds are set for accurate reading from 20815 sensor (reads accurately from 5cm to 80cm)
    //case 'd' 'e' 'f' dist_low2 and dist_high2 bounds are set for accurate reading from MAXSONAR sensor (reads accurately from 20cm to 95cm)
      switch (data.id){
        /*************************************************************************************************************************/
        case 'a':
        data1=data.cm;
        if (data.cm<=80&&data.cm!=0){
          val= map(data.cm, dist_low, dist_high,motor_high,motor_low); //mapping val to minimum and maximum(Change if needed) 
        }
        else{
          val=val_default;
        }
        //Serial.println(val);
        esc.writeMicroseconds(val);
        break;
        /****************************************************************************************************************************/
        case 'b':
        data2=data.cm;
        if (data.cm<=80&&data.cm!=0){
       val2= map(data.cm, dist_low, dist_high,motor_high,motor_low); //mapping val to minimum and maximum(Change if needed) 
       }
        else{
        val2=val_default;
        }
        esc2.writeMicroseconds(val2);
        break;
        /**********************************************************************************************************************************/
        case 'c':
        data3=data.cm;
        if (data.cm<=80&&data.cm!=0){
       val3= map(data.cm, dist_low, dist_high,motor_high,motor_low); //mapping val to minimum and maximum(Change if needed) 
       }
        else{
        val3=val_default;
        }
        esc3.writeMicroseconds(val3);
        break;
        /**********************************************************************************************************************************/
        case 'd':
        data4=data.cm;
        if (data.cm<=95&&data.cm>=20){
          val4= map(data.cm, dist_low2, dist_high2,motor_high,motor_low); //mapping val to minimum and maximum(Change if needed) 
        }
        else{
          val4=val_default;
        }
        //Serial.println(val);
        esc4.writeMicroseconds(val4);
        break;
        /******************************************************************************************/
        case 'e':
        data5=data.cm;
        //rssi5=-20*log(t)/log(10);
        if (data.cm<=95&&data.cm>=20){
       val5= map(data.cm, dist_low2, dist_high2,motor_high,motor_low); //mapping val to minimum and maximum(Change if needed) 
       }
        else{
        val5=val_default;
        }
        esc5.writeMicroseconds(val5);
        break;
        /**********************************************************************************************************************************/
        case 'f':
        data6=data.cm;
        if (data.cm<=95&&data.cm>=20){
       val6= map(data.cm, dist_low2, dist_high2,motor_high,motor_low); //mapping val to minimum and maximum(Change if needed) 
       }
        else{
        val6=val_default;
        }
        esc6.writeMicroseconds(val6);
        break;
        /**********************************************************************************************************************************/     
}
Serial.print(data1);
Serial.print(",");
Serial.print(data2);
Serial.print(",");
Serial.print(data3);
Serial.print(",");
Serial.print(data4);
Serial.print(",");
Serial.print(data5);
Serial.print(",");
Serial.print(data6);
Serial.print("\n"); 
  //you should make this delay shorter then your transmit delay or else messages could be lost
  delay(100);
}
}

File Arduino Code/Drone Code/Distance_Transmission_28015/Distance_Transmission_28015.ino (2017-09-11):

/*
This is for transmitting data through the Easy Transfer Library to the flying maze. The distance is measured from the ultrasonic sensor and sent through the XBee.  The microseconstocentimeters function and getduration were written for the Parallax 28015 REV B ultrasonic
sensor. This code was written for Teensy 3.0 and Teensy LC. Other versions of Teensy or Arduino may require the 
Serial3 to be changed. 
*/

//LINK for the EasyTranfer library download: 
//http://www.billporter.info/2011/05/30/easytransfer-arduino-library/
//     for easy data tranfer using packets

#include <EasyTransfer.h>

const int pingPin1 = 14;
float duration1;

EasyTransfer ET; //creates object

struct SEND_DATA {   //puts all the variables inside a struct to send a packet of data

  char id='b';//change this character based on which sending setup this code is loaded on a-b-c-d-e-f 

  float cm; 
};

SEND_DATA data; //creates a variable that i can use in loop

void setup()
{
  //Begin serial monitor port on transmitting end
  Serial.begin(9600);
  Serial3.begin(9600);
  //Begin HW serial
  ET.begin(details(data), &Serial3); //opens serial port between the xbees
}

float microsecondsToCentimeters(float microseconds) {
  // The speed of sound is 340 m/s or 29 microseconds per centimeter.
  // The ping travels out and back, so to find the distance of the
  // object we take half of the distance travelled.
  return microseconds / 29 / 2;
}

float getDuration(int pingPin)
{
  //Code to read in the Ping sensor value
  pinMode(pingPin, OUTPUT);
  digitalWrite(pingPin, LOW);
  delayMicroseconds(2);
  digitalWrite(pingPin, HIGH);
  delayMicroseconds(5);
  digitalWrite(pingPin, LOW);
  pinMode(pingPin, INPUT);
  
  float duration = pulseIn(pingPin,HIGH);
  return duration;
}
void loop() {
  // put your main code here, to run repeatedly:
  // Take data received from the serial monitor and pass it to the HW UART 
  duration1 = getDuration(pingPin1);
  data.cm = microsecondsToCentimeters(duration1); //1st sensor distance value
  
  //send the data
  ET.sendData();

  //printing the data to my serial monitor
  Serial.println(data.cm);
  //Serial.print(", ");

  //printing data to the other serial monitor on the recieving end
  //Serial3.print(data.cm); //This line is not needed since EasyTransfer library is being used
  
  delay(250); // Wait to reduce serial load
}

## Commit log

2017-07-11 I restructured the folders
    [Maze_completed.f3d, Maze_completed.stl]
2017-07-11 moved both distance transmission arduino code files to drone file
2017-07-12 Added a test motor test program to test flight ability of the drone
2017-07-18 Added complete .f3d smith chart
    [Maze_completed.f3d, Maze_completed.stl, Resizable_Smith_Chart_Complete_7-18.f3d]
2017-07-20 Added final SMmith M Maze Design
    [SMITH_FINAL_MODEL v0.f3d]
2017-08-03 Edited the ending print statments
2017-08-03 Edited the edning print statements
2017-08-03 Edited ending print statements
2017-08-07 Add files via upload
    Graphing sensor data
2017-08-07 Graphing sensor data
2017-08-08 Created a folder for 3D CAD files
    [Sensor_Enclosure-v3.0.stl, lid_for_box3.0.stl]
2017-09-11 Added Drone Documentation Readme
    [Assem2STL - Part9^Assem2-1.STL, Maze_Cone.stl, Resizable_Smith_Chart_Complete_7-18.f3d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]
2017-10-23 Create 3D printed Parts Documentation.md
2017-10-23 Added the Cone stl and the mounting base stl
    [Bottom Mount.stl, Cone Top.stl]
2017-10-23 Update 3D printed Parts Documentation.md
